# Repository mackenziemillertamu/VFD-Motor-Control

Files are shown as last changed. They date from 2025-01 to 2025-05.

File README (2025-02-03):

"Your project should have a README file that explains the project and what is contained in the repository"

Traditional motor control systems cannot adjust to varying load demands, resulting in poor energy efficiency, excessive heat generation, and premature component failure. Our project is to develop a Variable Frequency Drive (VFD) motor control system to adjust frequency and voltage to load demands. 

This github repository includes altium files, firmware code files, presentations pdfs, and report pdfs to act as a backup of our progess in the event of an emergency.

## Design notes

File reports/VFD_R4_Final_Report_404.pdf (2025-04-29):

# VFD Motor Controller

# Mackenzie Miller Andrew Nguyen Aidan Rader Ryan Regan

# CONCEPT OF OPERATIONS

### REVISION – 1 28 April 2025

### CONCEPT OF OPERATIONS

### FOR

## VFD Motor Controller

TEAM VFD MOTOR CONTROLLER

APPROVED BY:

_____________________________
Project Leader | Date

_____________________________
Prof. Lusher | Date

_____________________________
T/A | Date

Concept of Operations | Revision 1
VFD Motor Controller

II

### Change Record

Rev. | Date | Originator | Approvals | Description
0 | 9/15/2024 | VFD Motor Controller Team | | Draft Release
1 | 4/28/2025 | VFD Motor Controller Team | | Final Report Update

Concept of Operations | Revision 1

III

### Table of Contents

Table of Contents | III
List of Figures | IV

Concept of Operations | Revision 1

IV

### List of Figures

Concept of Operations | Revision 1

## 1. Executive Summary

The sponsor for this project is in need of a VFD motor controller for an AC induction motor. The VFD will control the speed and torque of the AC motor. This project will help to increase energy efficiency by ensuring that the motor isn’t running at a higher speed than necessary. It also makes the system more reliable and sustainable by decreasing mechanical stress.

A Variable Frequency Drive (VFD) is a device that controls the speed of an electric motor by varying the frequency of the delivered voltage. VFDs are useful because they improve the energy efficiency, reliability, safety, stability, and controllability of a motor. The goal of this project is to make a VFD motor controller that will efficiently control the seed and torque of an electric motor.

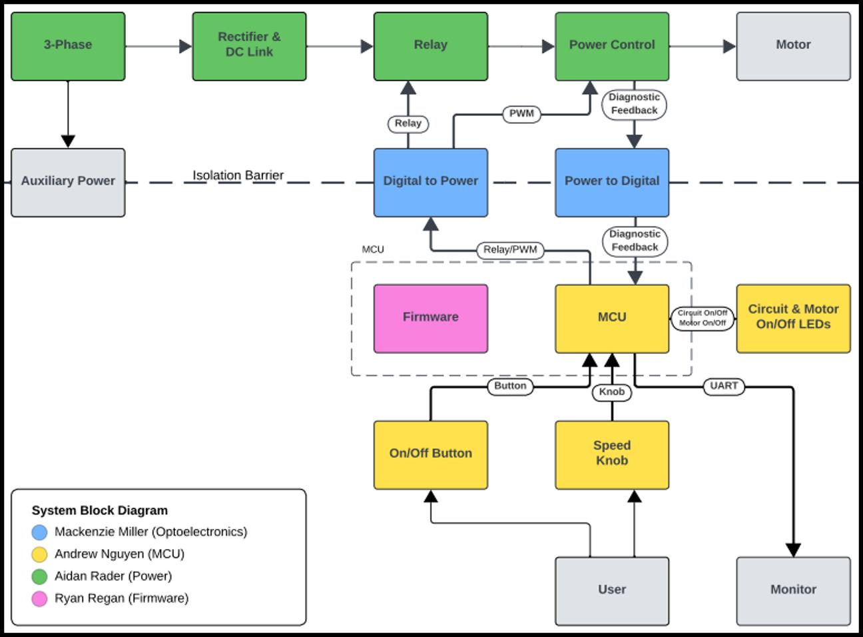
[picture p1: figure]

Figure 1: VFD Motor Controller Block Diagram

Concept of Operations | Revision 1

## 2. Introduction

### 2.1 Background

VFD motor controllers have several beneficial functionalities that can improve the quality of a system. A VFD motor controller regulates the speed and torque of electric motors by controlling the frequency and voltage supplied. The speed is controlled by varying the frequency of the supply of electricity. It also allows for more efficient systems. By running at certain speeds, the VFD can reduce the power consumed, allowing for energy to be saved. It also reduces stress on the motor by allowing for soft starting and stopping. The VFD also has a functionality allowing it to shut off the motor if something is shorted, overheating, or overloaded. The VFD will replace a fixed speed motor in a mechanical system.

### 2.2 Overview

While fixed speed motor controllers are still useful in some applications, more often than not a VFD motor controller is a better alternative. It offers all the functionality of a fixed speed motor controller while also being able to vary the speed and torque of the motor if needed. In this project, our team will work to create a Variable Frequency Drive to control motor speed. In addition, we will consider several different factors such as user interface for the drive, and implementation of the drive in a closed and open loop. This upgrade will improve the energy efficiency, reliability, safety, stability, and controllability of the motor.

### 2.3 Referenced Documents and Standards

“The Advantages of Frequency Drive Operation in Submersible Pumps.” Grundfos, www.grundfos.com/us/learn/ecademy/all-courses/the-sp-submersible-pump/the-advantages-of-frequency-drive-operation-in-submersible-pumps. Accessed 15 Sept. 2024.
By, and Dosupply. “What Do VFDS DO in HVAC Systems?: Do Supply Tech Support.” Do
Supply Tech Support | Information and Troubleshooting on Allen-Bradley, Eaton, GE
Fanuc, and More, 11 Aug. 2022, www.dosupply.com/tech/2022/08/11/what-do-vfds-do-in-hvac-systems/. (http://www.dosupply.com/tech/2022/08/11/what-do-vfds-do-in-hvac-systems/)

Hoffman, Theresa. “What Are the Benefits of a Variable Frequency Drive?” Wolf Automation,www.wolfautomation.com/blog/what-are-the-benefits-of-a-variable-frequency-drive/. Accessed 15 Sept. 2024.

“Variable Frequency Drive for Conveyor and Material Handling.” Variable Frequency Drive for Conveyor and Material Handling-Darwin Motion, darwinmotion.com/blogs/variable-frequency-drive-for-conveyor-and-material-

Concept of Operations | Revision 1

handling#:~:text=The%20use%20of%20a%20Variable,belt%20speed%2C%20reducin g%20energy%20consumption. Accessed 15 Sept. 2024.

IEEE 519-2014 Standard for Harmonics

Concept of Operations | Revision 1

## 3. Operating Concept

### 3.1 Scope

The VFD motor controller is intended to control the speed and torque of an AC motor by varying the frequency and voltage supplied. This project will use three phase power as the input that will be converted to DC and then transmitted to a microcontroller via optoelectronics and used to power a motor. The microcontroller also will send signals to the DC link, again using optoelectronics, that contain the desired frequency specified by the user on the user interface. This VFD shall be implemented to increase efficiency and save energy.

### 3.2 Operational Description and Constraints

The VFD motor controller is designed to vary the frequency and voltage supplied to an AC motor to control its speed and torque. It converts a three-phase AC input into DC using a rectifier and transmitting the power using a microcontroller.
- Microcontroller Function
- The microcontroller is responsible for generating pulse-width modulation (PWM) signals which are used to adjust the frequency and voltage supplied to the motor.
- The user can set the desired motor speeds via the user interface or the code itself. The microcontroller then ensures that the motor is running according to its specifications.
- Optoelectronics
- LED lights are used to communicate between the high-voltage power components and the low-voltage microcontroller. This ensures that the signals are safely transmitted.
- User Interface
- The microcontroller will have a potentiometer that allows the user to change the frequency of the three-phase PWM signal that is being output to the motor.
- While the PCB is plugged into a computer, opening the output terminal in MPLab will allow the user to view debug statements such as the potentiometer’s value, output duty cycles to phases A, B, and C, sine wave table step size, and desired output frequency of the PWM sine wave.
- Constraints:
- Sustainability
- Humidity, dust, and temperatures outside of the specified range can cause the VFD to malfunction.
- Noise levels
- The VFD is noise sensitive and is susceptible to external electrical noise, which could decrease the reliability of the system.

Concept of Operations | Revision 1
- Power
- The VFD requires stable three-phase AC power. Spikes or fluctuations could damage some of the system’s components.
- Mechanical wear and maintenance
- All parts of the VFD are subject to general mechanical wear and tear over time, especially if operated under high loads or in challenging environments.
- Cost and installation
- The VFD system can be expensive to produce, especially when considering large-scale applications. Consideration must be given to the specific needs of the project

### 3.3 System Description

The VFD motor controller is comprised of a DC link (includes a rectifier and DC bus), power controller, microcontroller, and optoelectronics. The DC link converts AC input into DC and minimizes the noise of the DC signal. The power controller controls the voltage. The microcontroller is used to produce PWM signals that will drive the motor. Optoelectronics allows for communication between the high voltage side and the low voltage microcontroller.
This is a four-person project, and the roles are be split into:
- Firmware:
- Write code in C with MPLAB that programs the microcontroller so that it functions with the rest of the VFD system according to desired specifications.
- Use a potentiometer to allow user to change the frequency of three-phase PWM signal.
- Print debug and feedback signals to UART console to allow for even further debugging.
- Test program on development board to ensure functionality then ensure proper integration with the project’s microcontroller.
- Optoelectronics
- The first part of the optoelectronics portion includes two isolation circuits. One of those takes digital signals in and directly converts them to analog. The second, being more complicated, takes analog input, then, using an optoisolator, the circuit converts the input to digital signals to be sent to the microcontroller. The analog side of the project works with very high voltage, while the digital side works with low voltage. Because of this, the two sides cannot be connected or the microcontroller will be overpowered and break, so the optoelectronics send signals and data across using light.
- The second part of the sensors portion is a constant current and voltage measurement. This will be done using a current sensing resistor, which has a

Concept of Operations | Revision 1

very small resistance, and a simple voltage divider circuit. These measurements will then be sent back to the firmware.
- Microcontroller:
- The MCU board is supplied by taking in the 120VAC from the wall and using an AC/DC converter to step it down to 15VDC. The voltage is then stepped down once more using the LM2595s-3.3 buck converter to a usable 3.3V that the MCU can handle. It receives feedback through low-voltage analog signals that represent voltage and current. The MCU will then send out PWM signals to the H bridge and power control system which are used to adjust the output voltage and frequency supplied to the motor. The board will also supply the optoelectronics subsystem with a common GND and 3.3V, and the power subsystem with a common GND, 15V, and 3.3V.
- Power:
- The rectifier takes in three-phase AC power and converts it into DC power. For each phase, there are parallel diodes acting as a one-way bridge for the current allowing it to flow in only one direction. To maintain the correct current polarity the diode opens and closes in sequence as the AC waveform alternates. The DC output is then filtered by capacitors within the DC link to provide a stable DC voltage for the microprocessor.
- The power control will take the DC power and the PWM signals and output three modified sign waves at 120 degrees to the motor. It will also output three measurement signals that can be used as diagnostic feedback: voltage, current, temperature
- The relay will take in a relay signal originating by the button press on the microcontroller and toggle the motor between on and off states.
- Converters will be used as part of auxiliary power to generate the necessary voltage levels for the different integrated chips. The two converters on the power PCB with be a 3.3 VDC to isolated 5 VDC converter and a 15 VDC to isolated 15 VDC.

### 3.4 Modes of Operations

There are two primary modes of operation for the variable frequency drive:
On: The motor receives 10-60Hz PWM signals depending on the position of the potentiometer located on the microcontroller PCB. The frequency of the PWM signals changes the speed of the motor.
Off: The relay is tripped, and the motor is no longer receiving any power.

### 3.5 Users

The potential user for our VFD would be a plant operator or manager. The goal is to have it set up to ensure a seamless installation and programming process for use in a closed or open

Concept of Operations | Revision 1

loop. It is assumed that a plant operator would know and understand what a VFD is and what it does. There will be simple controls that the user can change to make the VFD do what they want it to do such as a potentiometer for controlling the frequency of output signals, and a start/stop button.

### 3.6 Support

We plan to create a manual describing what the VFD does and how to use it. The VFD will support usage, programming, and debugging through MPLAB X IDE. It will allow the user to control the motor’s on/off function and its speed while showing the user several different variables including the measured motor speed from the tachometer.

Concept of Operations | Revision 1

## 4. Scenario(s)

### 4.1 HVAC

VFDs can be extremely useful in a Heating, Ventilation, and Air Conditioning (HVAC) system. VFDs can act as speed controllers for HVAC motors because they actively adjust the speed rate of those motors based on the building load demands. Without a VFD, an HVAC system will run at full power regardless of whether the system requires full power at that time. By running only as powerful as needed, energy and money are saved. Additionally, a VFD allows an HVAC motor to slowly get up to the full speed which is called a “soft start”. This lessens wear and tear on these HVAC motors, which helps them to last longer and saves money. VFDs can help HVAC systems to control temperature and pressure, among other measurements in a building, they help to save energy and extend the life of HVAC motors.

### 4.2 Conveyor Belt

In conveyors for production lines, a VFD allows an operator to control the belt's speed to match the production line's needs. This ensures that the belt is not moving too slow to decrease efficiency or too fast to risk injuring employees and consume copious amounts of energy. Wear and tear is also decreased by being able to run the belt at the most appropriate speed as to not overwork the parts or run the belt for too long. The slow start that a VFD can offer helps to reduce wear and tear on the conveyor parts so they can gradually get up to speed. There is the ability to gradually slow down the belt when turning off, which also extends the life of equipment. The VFD increases energy efficiency and reduces maintenance which both save money.

### 4.3 VFD Pump

VFDs are sought after for submersible pumps for several applications. The main benefit of a VFD in a water pump is the ability to keep a certain parameter constant. VFDs are commonly used in construction sites to keep groundwater at a constant level to build. The VFD does this by adjusting the speed of the motor controlling the water pump. Additionally, VFDs are useful in maintaining constant pressure in a water tank. VFDs are crucial in the operation of water pumps across many different disciplines because their speed control allows for constant parameters in the specified system.

Concept of Operations | Revision 1

## 5. Analysis

### 5.1 Summary of Proposed Improvements

Improvements:
- Extended life of parts: being able to vary frequency and torque help to reduce overloading equipment and, in turn, makes them last longer
- Increased efficiency: instead of a system having to run at a constant speed, a VFD allows the system to run only as fast as needed, which reduces energy consumption, and saves money
- Limits safety risks: having a system run at the proper speed and maintain a safe amount of torque helps decrease the risk of injury

### 5.2 Disadvantages and Limitations

Disadvantage:
- VFD can damage motor windings and bearings
- Can ruin insulation
- Creates harmonics (potentially interfering with communications and data processing)
- Can be very expensive
- Is prone to overheating if not in a properly ventilated area.
- Can create voltage spikes which could ruin the motor.

### 5.3 Alternatives

Alternatives to a VFD:
- Eddy Current Drive: induces a magnetic field that is adjustable to control the speed of a motor
- Soft Starters: Soft starters gradually increase the voltage to an AC motor during startup to reduce damage. They provide a more economical choice for applications where torque and speed control are only required during motor startup and stop.
- Cycloconverters: Cycloconverters convert the frequency of AC power from one frequency to another without having to convert to DC and back to AC. They are typically used in applications that require low speeds and high torque. This is a good alternative for when direct frequency conversion is more suitable than VFDs.

### 5.4 Impact

One environmental impact of a VFD is the ability to lower greenhouse gas emissions. By increasing the motor's energy efficiency through frequency adjustments to match load requirements, VFDs decrease the emissions released during the energy generation process.

Concept of Operations | Revision 1

A second environmental impact of a VFD is the degradation caused by mining the raw materials. While mining procures the rare metals needed for electronics, it also causes deforestation from the removal of forests, soil erosion from the disruption of the soil structure, and air pollution from the diesel emissions and dust particles generated by the machinery.

Another environmental impact of a VFD is the end-of-life disposal of electronic waste. Disposal of electronics can be challenging and, if done improperly, can contaminate soil and water with toxic metals. Alternatively, VFDs reduce this risk by reducing equipment wear, extending replacement intervals, and reducing disposal frequency.

A social impact of a VFD is the change in employment opportunities. The automation of the VFD reduces the need for operators who manually control the motor speed. Conversely, VFDs generate new roles including engineers who design the systems, miners who extract the raw materials, factory workers who assemble the components, and technicians who handle the maintenance.

Another social impact of a VFD is the safety risks. The VFD's automation of motor control within safe torque limits reduces the risk of accidents or injuries. However, if the VFD is improperly insulated or maintained, high voltages can pose a risk of electrical shock, and insulation breakdowns can pose a risk of short circuits and fire.

One ethical concern of a VFD is supply chain transparency. The raw materials for VFDs are often sourced from mines in countries with varying labor laws. In these mines, workers may face safety risks, including interacting with hazardous chemicals and dangerous machinery. Additionally, these mines should also avoid exploitative practices, including unfair compensation and unreasonable working hours.

A second ethical concern of a VFD is testing sufficiency. Before bringing a VFD to market, it should meet safety standards and demonstrate reliable operation. The testing process should include quality construction to prevent defects, comprehensive testing to identify defects, and clear documentation to resolve defects.

# VFD Motor Controller

# Mackenzie Miller Andrew Nguyen Aidan Rader Ryan Regan

# INTERFACE CONTROL DOCUMENT

### REVISION – 0 26 September 2024

### INTERFACE CONTROL DOCUMENT

### FOR

## VFD Motor Controller

PREPARED BY:

_____________________________
Author | Date

APPROVED BY:

_____________________________
Project Leader | Date

_____________________________
John Lusher II, P.E. | Date

_____________________________
T/A | Date

Interface Control Document | Revision - 0

II

### Change Record

Rev. | Date | Originator | Approvals | Description
0 | 9/26/2024 | VFD Motor Controller Team | | Draft Release
1 | 12/5/2024 | VFD Motor Controller Team | | Microcontroller and firmware descriptions updated
2 | 4/28/2025 | VFD Motor Controller Team | | Final Report Update

Interface Control Document | Revision - 0

III

### Table of Contents

Table of Contents | III
List of Tables | IV
List of Figures | V
No table of figures entries found | V

Interface Control Document | Revision - 0

IV

### List of Tables

Interface Control Document | Revision - 0

V

### List of Figures

No table of figures entries found.

Interface Control Document | Revision - 0

## 1. Overview

This Interface Control Document (ICD) for the VFD Motor Controller provides an overview of the requirements and specifications for a Variable Frequency Drive that will be used to control a motor and it’s speed. Created by Ryan Regan, Andew Nguyen, Mackenzie Miller, and Aidan Rader, this document describes the physical, electrical, thermal, and communication interfaces for the system.

Key Sections:
- Physical Interface: This section depicts the physical aspects of the VFD including weight, dimensions, and physical/spatial requirements.
- Thermal Interface: The VFD includes a thermal monitoring system using the VFO pin and ITRIP pins that will shut the system down if the temperature levels are too high
- Electrical Interface: The electrical specifications include motor power, DC supply voltage, and the microcontroller’s stepped-down voltage supply. The DC voltage will be regulated by an H-bridge, and optoelectronic circuits will be used to isolate the microcontroller from the high voltage section of the system.
- User Interface: The VFD’s firmware allows the user to control the on/off functionality of the system as well as the speed of the motor with a button and potentiometer. The microcontroller can be plugged into a computer to view other different diagnostic feedback variables from the system.
- Communication Protocols: Optoelectronics will be used for communication between the high-voltage power control and the low-voltage microcontroller. Additionally, the system will use UART for serial communication and will have USB connectivity for programming and debugging.

Interface Control Document | Revision - 0

## 2. References and Definitions

### 2.1 Definitions

AC | Alternating Current
DC | Direct Current
GUI | Graphical User Interface
ICD | Interface Control Document
MHz | Megahertz (1,000,000 Hz)
MCU | Micro Controller Unit
mA | Milliamp
mW | Milliwatt
N/A | Not Applicable
TBD | To Be Determined
VFD | Variable Frequency Drive

Interface Control Document | Revision - 0

## 3. Physical Interface

### 3.1 Weight

The VFD motor controller may weigh up to 6lbs. The motor itself may weigh up to 13lbs.

### 3.2 Dimensions

### 3.2.1 Dimension of Optoelectronics and Feedback

Component | Diameter | Length | Width | Height
Digital Isolator | N/A | 0.406” | 0.406” | 0.104”
Analog to Digital Optoisolator | N/A | 0.442” | 0.354” | 0.158”
Operational Amplifier | N/A | 0.382” | 0.25” | 0.400”
12 Pin Connector | N/A | 0.854” | 0.389” | 0.271”
8 Pin Connector | N/A | 1.089” | 0.447” | 0.272”

### 3.2.2 Dimensions of MCU

Component | Diameter | Length | Width | Height
dsPIC33CK256MP508 | N/A | 0.394” | 0.394” | 0.039”
LM2595s-3.3 Buck Converter | N/A | 0.400” | 0.180” | 0.450”
IRM 15-15 AC/DC Connector | N/A | 2.06” | 1.07” | 0.945”
20 Pin connector | N/A | 1.68” | 0.276” | 0.335”
5 Pin Connector | N/A | 0.314” | 0.433” | 0.370”
3 Pin Connector | N/A | 0.600” | 0.322” | 0.393”
Potentiometer | 0.236” (actuator) | 0.433” | 0.386” | 1.173”

The physical dimensions of the subsystem will be relative to the size of the user’s laptop and the size of the motor, both should not exceed the size of a standard tabletop.

### 3.2.3 Dimensions of Rectifier & DC Link

Component | Diameter | Length | Width | Height
VUE75-06NO7 | N/A | 1.850” | 1.193” | 0.799”
IKCM30F60GD | N/A | 1.417” | 0.827” | 0.201”
Capacitor(s) | N/A | TBD | TBD | TBD
Inductor(s) | N/A | TBD | TBD | TBD

Table 1: Optoelectronics and Feedback Dimensions

Table 2: MCU Dimensions

Table 3: Rectifier & DC Link Dimensions

Interface Control Document | Revision - 0

## 4. Thermal Interface

### 4.1 Temperature Sensing

The power control shall monitor the temperature via the VFO pin, and if the VFD temperature rises above a safe value, the ITRIP pin will automatically shut the project down to avoid damaging parts.

Interface Control Document | Revision - 0

## 5. Electrical Interface

### 5.1 Primary Input Power

The motor being used is 0.25HP producing 186.425W of power. The voltage supplied to the system is 295VDC which is then taken in by the H-bridge to generate a line-to-line voltage of 208V. 15VDC power is supplied to the MCU from the AC/DC power supply fed by the main power. This voltage will be stepped down to 3.3V for the MCU to use.

### 5.2 Voltage and Current Levels

Component | Voltage (V) | Current (mA)
dsPIC33CK | 3.3V | 50mA
IKCM30F60GD | 600V | 60A

### 5.3 Signal Interfaces

Pulse Width Modules will be sent from the microcontroller to the power control of the VFD project using optoelectronic circuitry to ensure the microcontroller does not come into contact with the high voltage in the power control.
Three phase voltage values will be sent to the microprocessor from the power control using optoelectronic circuitry to ensure that the microprocessor does not come into contact with the high voltage in the power control.

### 5.4 User Control Interface

One feature of the VFD’s microcontroller will be a potentiometer that allows the user to control the frequency of the three phase PWM’s sine wave by increasing the step size that the program uses to step through a sine wave table. Increasing the PWM signal’s frequency will increase the speed of the motor. The user will be able to change the frequency by turning a potentiometer. Another feature of the microcontroller is the start/stop button. This will give the user the option to turn the motor on and off without having to disconnect the system’s power. In addition to the physical user interface, the VFD will display several debug variables to the UART console in MPLAB X IDE when connected to a computer. The user will be able to view the voltage, current, and temperature in a UART console.

Table 4: Maximum Voltage and Current Values

Interface Control Document | Revision - 0
Pin | Function
1 | PWM1H
2 | GPIO
3 | PWM1L
4 | GPIO
9 | MCLR
11,32,50,70 | VSS
12,31,51,71 | VDD
17,22,39,44 | GPIO
19 | GPIO (Potentiometer)
24 | GPIO (LED 2)
25 | AVDD
26 | AVss
34 | Clock input
37 | GPIO (LED 1)
42 | GPIO (Relay)
60 | PGD1
61 | PGC1
68 | UART TX
69 | UART RX
75 | PWM3H
76 | PWM3L
78 | PWM2H
80 | PWM2L

Table 5: Pin interface for DSPIC33CK256MP508 Microcontroller

Interface Control Document | Revision - 0

## 6. Communications / Device Interface Protocols

### 6.1 Optoelectronic Communications

The high voltage power control of the VFD will communicate to the low voltage or MCU via optoelectronics, or light to ensure that the MCU is not overpowered by the 120 VAC in the analog power control side.

### 6.2 Firmware and MCU Communications

The microcontroller is programmed with C code through MPLab’s X IDE and will have several firmware implementations such as an on/off button’s functionality and a three-phase PWM wave’s frequency control.

### 6.3 Device Peripheral Interface

The MCU will use UART interface for serial communication between devices. This is what will allow a laptop to communicate with the microcontroller through USB connection.

### 6.4 Host Device

The C code shall be ran on MPLab’s X IDE, which should be downloaded on the users computer. This will be used to program the microcontroller and output any debug variables necessary while the system is running.

# VFD Motor Controller

# Mackenzie Miller Andrew Nguyen Aidan Rader Ryan Regan

# FUNCTIONAL SYSTEM REQUIREMENTS

### REVISION – 1 28 April 2025

### FUNCTIONAL SYSTEM REQUIREMENTS

### FOR

## VFD Motor Controller

PREPARED BY:

_____________________________
Author | Date

APPROVED BY:

_____________________________
Project Leader | Date

_____________________________
John Lusher, P.E. | Date

_____________________________
T/A | Date

Functional System Requirements | Revision - 1

II

### Change Record

Rev. | Date | Originator | Approvals | Description
0 | 9/26/2024 | VFD Motor Controller Team | | Draft Release
1 | 12/5/2024 | VFD Motor Controller Team | | Reference documents updated
2 | 4/28/2025 | VFD Motor Controller Team | | Final Report Update

Functional System Requirements | Revision - 1

III

### Table of Contents

Table of Contents | III
List of Tables | IV
List of Figures | V

Functional System Requirements | Revision - 1

IV

### List of Tables

Functional System Requirements | Revision - 1

V

### List of Figures

Functional Requirements Document | Revision 0
VFD Motor Control

## 1. Introduction

### 1.1. Purpose and Scope

The VFD motor controller is intended to control the speed and torque of an AC motor by varying the frequency and voltage supplied. This project will use three phase power as the input that will be converted to DC and then transmitted to a microcontroller via optoelectronics and used to power a motor. The microcontroller also will send signals to the DC link, again using optoelectronics, that contain the desired frequency. The VFD motor controller will come with a user interface that allows the user to input the frequency needed and start or stop the system as needed. This VFD shall be implemented to increase efficiency and save energy.

The following definitions differentiate between requirements and other statements.

Shall: | This is the only verb used for the binding requirements.
Should/May: These verbs are used for stating non-mandatory goals.
Will: | This verb is used for stating facts or declaration of purpose.

### 1.2. Responsibility and Change Authority

Briefly describe who has the responsibility for making sure the requirements are met (i.e., team leader) and who has the authority to make the changes (i.e., client and team leader).

Figure 1: Project Conceptual Image

Functional System Requirements | Revision - 1
Subsystem | Team Member
Optoelectronics & Monitoring | Mackenzie Miller
Microcontroller | Andrew Nguyen
Rectifier & DC Link | Aidan Rader
Firmware | Ryan Regan
Table 1: Subsystem Designations

Functional System Requirements | Revision - 1

## 2. Applicable and Reference Documents

### 2.1 Applicable Documents

The following documents, of the exact issue and revision shown, form a part of this specification to the extent specified herein:

Document Number | Revision/Release Date | Document Title
IEEE 519-2014 | 3/27/2014 | Standard for Harmonics
NFPA 70 Article 430 | 08/8/2023 | Motors, Motor Circuits and Controllers

### 2.2 Reference Documents

The following documents are reference documents utilized in the development of this specification. These documents do not form a part of this specification and are not controlled by their reference herein.

Document Number/ Publisher | Revision/Release Date | Document Title
Microsemi | Revision 0/11-03-2005 | DM330030 Datasheet
Microchip Technology | Revision 11/06-2022 | dsPIC33CK256MP508 Family Data Sheet
Texas Instruments | Revision 3/05-2016 | LM2595 SIMPLE SWITCHER® Power Converter 150-kHz 1-A Step-Down Voltage Regulator datasheet
Skyworks | Revision B/09-2023 | Si861x/2x Low-Power, Single- and Dual-Channel Digital Isolator
Infineon | Revision 2019-10-16 | Control Integrated POwer System (CIPOS™) IKCM30F60GD
IXYS | Revision 2021 | VUE75-06NO7
Mean Well | Revision 10-30-2024 | IRM-15 series Datasheet

### 2.3 Order of Precedence

In the event of a conflict between the text of this specification and an applicable document cited herein, the text of this specification takes precedence without any exceptions.

All specifications, standards, exhibits, drawings or other documents that are invoked as “applicable” in this specification are incorporated as cited. All documents that are referred to within an applicable report are for guidance and information only, except ICDs that have their relevant documents considered to be incorporated as cited.

Table 2: Applicable Documents

Table 3: Reference Documents

Functional System Requirements | Revision - 1

## 3. Requirements

### 3.1 System Definition

The VFD motor controller is comprised of a DC link (includes a rectifier and DC bus), power controller, microcontroller, and optoelectronics. The DC link converts AC input into DC and minimizes the noise of the DC signal. The power controller controls the voltage. The microcontroller is used to produce PWM signals that will drive the motor. Optoelectronics allows for communication between the high voltage side and the low voltage microcontroller.
This is a four-person project split into these roles:

Firmware (Ryan Regan):
Write code in C using MPLab X IDE that programs the microcontroller so that it functions with the rest of the VFD system according to desired specifications. In other words, program a potentiometer to allow user to change the frequency of a three-phase PWM signal. The firmware will also implement debug statements that output to MPLAB X IDE’s UART console to allow user to view different variables as the program is running. Before integrating with the microcontroller and other subsystems, the firmware will be tested on a development board to ensure functionality.

Optoelectronics (Mackenzie Miller):
The first part of the sensors portion includes two optoelectronic circuits. One of those takes digital signals in and directly converts them to analog. The second, being more complicated, takes analog input, then, using an opto-isolator, the circuit converts the input to digital signals to be sent to the microcontroller. The analog side of the project works with very high voltage, while the digital side works with low voltage. Because of this, the two sides cannot be connected or the microcontroller will be overpowered and break, so the optoelectronics send signals and data across using light. The second part of the sensors portion is a constant current and voltage measurement. This will be done using a current sensing resistor, which has a very small resistance, and a simple voltage divider circuit. These measurements will then be sent back to the firmware. Finally, there will be a tachometer that measures the RPMs of the motor that is also sent to the firmware.

Microcontroller (Andrew Nguyen):
The MCU is supplied by the 15 VDC from the AC power supply fed by the main power. The voltage will then be stepped down to a usable 3.3V. It receives feedback through low-voltage analog signals that represent voltage and current. The MCU will then send out PWM signals to the H bridge and power control system which are used to control the inverter stage of the VFD which helps to adjust the output voltage and frequency supplied to the motor.

Rectifier and DC Link (Aidan Rader):

Functional System Requirements | Revision - 1

The rectifier takes in three-phase AC power and converts it into DC power. For each phase, there are parallel diodes acting as a one-way bridge for the current allowing it to flow in only one direction. To maintain the correct current polarity the diode opens and closes in sequence as the AC waveform alternates. The DC output is then filtered by capacitors within the DC link to provide a stable DC voltage for the microprocessor.

### 3.2 Characteristics

### 3.2.1 Functional / Performance Requirements

### 3.2.1.1 Speed and Torque Requirement

The 0.25HP VFD motor shall run up to 1800RPM. The torque requirement for this is 73lb-ft of torque.

### 3.2.1.2 Frequency Requirement

The VFD motor controller shall be able to handle frequencies from 5Hz to 60Hz.

Figure 2: Block Diagram of System

Functional System Requirements | Revision - 1

Rationale: American standard frequency for alternating current

### 3.2.1.3 Temperature Requirement

The VFD motor controller shall be able to operate at temperatures ranging from 0°C to 70°C.
Rationale: Commercial temperature rating standards

### 3.2.2 Physical Characteristics

### 3.2.2.1 System Components

The system shall consist of three printed circuit boards (PCBs) connected by wires.

### 3.2.3 Electrical Characteristics

### 3.2.3.1 Inputs

The presence or absence of any combination of the input signals in accordance with ICD specifications applied in any sequence shall not damage the VFD motor controller, reduce its life expectancy, or cause any malfunction, either when the unit is powered or when it is not.

No sequence of command shall damage the VFD, reduce its life expectancy, or cause any malfunction.

Rationale: By design, should limit the chance of damage or malfunction by user/technician
error.

### 3.2.3.2 Input Voltage Level

The input voltage level for the VFD shall be three phase 120 VAC.
Rationale: VFD specification, Sponsor

### 3.2.3.3 Input Noise and Ripple

The maximum ripple allowed on the dsPIC33CK is 165mV peak to peak.
Rationale: The specifications from the dsPIC33CK datasheet at 3.3V

### 3.2.3.4 External Commands

The VFD Motor Control Team shall document all external commands in the appropriate ICD.
Rationale: The ICD will capture all interface details from the low level electrical to the high-level packet format.

### 3.2.3.5 Visual Output

The VFD shall include a Graphical User Interface that displays output measurements.
Rationale: Provides the ability to see the outputs when VFD is running

Functional System Requirements | Revision - 1

### 3.2.3.6 Connectors

The VFD shall use terminal blocks for all power and signal connections to ensure secure and vibration-resistant connections.
Rationale: Noise must be limited to maintain signal integrity

### 3.2.3.7 Failure Propagation 3.2.3.7.1 Overtemperature Shutdown

The VFD shall have a sensor that automatically shuts the system down if the temperature rises above 70 degrees Celsius.

### 3.2.3.8 Built in Test (BIT)

The VFD shall have an internal subsystem that will generate test signals and evaluate the VFD responses and determine if there is a failure.

### 3.2.3.9 Digital to Power Continuity

The digital to power opto-isolators shall have a voltage of 0V across each component when measuring from input to output.

### 3.2.3.10 Power to Digital Continuity

The power to digital opto-isolators shall have a voltage of 0V across each component when measuring from input to output.

3.2.3.11 15 VDC to Isolated 15 VDC Conversion
Power converters shall convert 15 VDC to isolated 15 VDC.

3.2.3.12 15 VDC to 3.3 VDC Conversion
Power converters shall convert 15 VDC to 3.3 VDC.

3.2.3.13 3.3 VDC to Isolated 5 VDC Conversion
Power converters shall convert 3.3 VDC to isolated 5 VDC.

### 3.2.3.14 Low Voltage Auxiliary Power

System shall convert 15 VDC to isolated 15 VDC , 3.3 VDC, and isolated 5 VDC.

3.2.3.15 120 VAC to 15 VDC Conversion
Power converters shall convert 120 VAC to isolated 15 VDC.

3.2.3.16 120 VAC Auxiliary Power
System shall convert 120 VAC to 15 VDC, isolated 15 VDC , 3.3 VDC, and isolated 5 VDC.

### 3.2.3.17 Relay

Relay shall toggle the motor with the relay signal.

### 3.2.3.18 Relay Signal Isolation

Digital to power shall convert the relay signal from 3.3 VDC to 5 VDC.

Functional System Requirements | Revision - 1

### 3.2.3.19 Relay Signal Generation

MCU shall toggle the relay signal to 3.3 VDC with the button signal.

### 3.2.3.20 Firmware Relay Signal Generation

Dev board shall toggle the relay signal to 3.3 VDC with the button signal.

### 3.2.3.21 Button Signal Generation

Button shall toggle the button signal to 3.3 VDC with a button press.

### 3.2.3.22 On/Off Button

System shall toggle the motor between on and off state with a button press.

3.2.3.23 120 VAC to 112 VDC Rectification
Rectifier shall convert 120 VAC to 112 VDC.

3.2.3.24 120 VAC to 112 VDC Rectification
Rectifier shall convert 120 VAC to 112 VDC.

### 3.2.3.25 Power Control

Power control shall invert three high and three low 5 VDC PWM signals into three modified sine waves.

### 3.2.3.26 PWM Signal Isolation

Digital to power shall convert three high and three low PWM signals from 3.3 VDC to 5 VDC.

### 3.2.3.27 PWM Signal Generation

MCU shall generate three high and three low 3.3 VDC PWM signals with the knob signal.

### 3.2.3.28 Knob Signal Generation

Rotating potentiometer changes frequency to speed up and slow down motor.

### 3.2.3.29 Firmware PWM Signal Generation

Dev board shall generate three high and three low 3.3 VDC PWM signals with the knob signal.

### 3.2.3.30 Firmware Knob Signal Generation

Rotating dev board potentiometer changes frequency to speed up and slow down motor.

### 3.2.3.31 Low Voltage PWM Control

System shall change the motor speed with the knob signal.

3.2.3.32 112 VDC PWM Control
System shall change the motor speed with the knob signal.

### 3.2.3.33 Motor On/Off Signal Generation

MCU shall toggle the motor on/off LED signal to 3.3 VDC with the button signal.

### 3.2.3.34 Motor On/Off LED

Functional System Requirements | Revision - 1

System shall toggle the motor on/off LED between on and off states with the motor on/off signal.

### 3.2.3.35 System On/Off Signal Generation

MCU shall toggle the circuit on/off LED signal to 3.3 VDC when the board receives power.

### 3.2.3.36 System On/Off LED

System shall toggle the circuit on/off LED when the board is connected to power with the circuit on/off signal

### 3.2.3.37 Firmware Motor On/Off LED Signal Generation

Firmware shall toggle the dev board's on/off LED signal to 3.3 VDC with the button signal.

### 3.2.3.38 Firmware Motor On/Off LED

Firmware shall toggle the dev board's on/off LED between on and off states with the motor on/off signal.

### 3.2.3.39 Firmware System LED Signal Generation

Firmware shall toggle the dev board's on/off LED signal to 3.3 VDC when the board receives power.

### 3.2.3.40 Firmware System LED

Firmware shall toggle the dev board's on/off LED when the board is connected to power with the circuit on/off signal

### 3.2.3.41 Computer Display

MCU will display diagnostic feedback information to the UART console on a computer running MPLAB X IDE

### 3.2.3.42 Diagnostic Feedback Signal Isolation

Diagnostic feedback circuit shall transport the voltage, current, and temperature signals from across the isolation barrier to the MCU.

### 3.2.3.43 Diagnostic Feedback Signal Generation

Power Control shall generate 60 VDC voltage, current, and temperature feedback signals.

### 3.2.3.44 Diagnostic Feedback

System shall send the voltage, current, and temperature signals to the computer display.

Functional System Requirements | Revision - 1

## Appendix A: Acronyms and Abbreviations

BIT | Built-In Test
CCA | Circuit Card Assembly
EMC | Electromagnetic Compatibility
EMI | Electromagnetic Interference
EO/IR | Electro-optical Infrared
FOR | Field of Regard
FOV | Field of View
GPS | Global Positioning System
GUI | Graphical User Interface
Hz | Hertz
ICD | Interface Control Document
kHz | Kilohertz (1,000 Hz)
LCD | Liquid Crystal Display
LED | Light-emitting Diode
mA | Milliamp
MHz | Megahertz (1,000,000 Hz)
MTBF | Mean Time Between Failure
MTTR | Mean Time To Repair
mW | Milliwatt
PCB | Printed Circuit Board
RMS | Root Mean Square
TBD | To Be Determined
TTL | Transistor-Transistor Logic
USB | Universal Serial Bus
VFD | Variable Frequency Drive
VME | VERSA-Module Europe

Functional System Requirements | Revision - 1

## Appendix B: Definition of Terms

# VFD Motor Controller

# Mackenzie Miller Andrew Nguyen Aidan Rader Ryan Regan

# EXECUTION AND VALIDATION PLAN

### REVISION – 1 28 April 2025

## Execution Plan

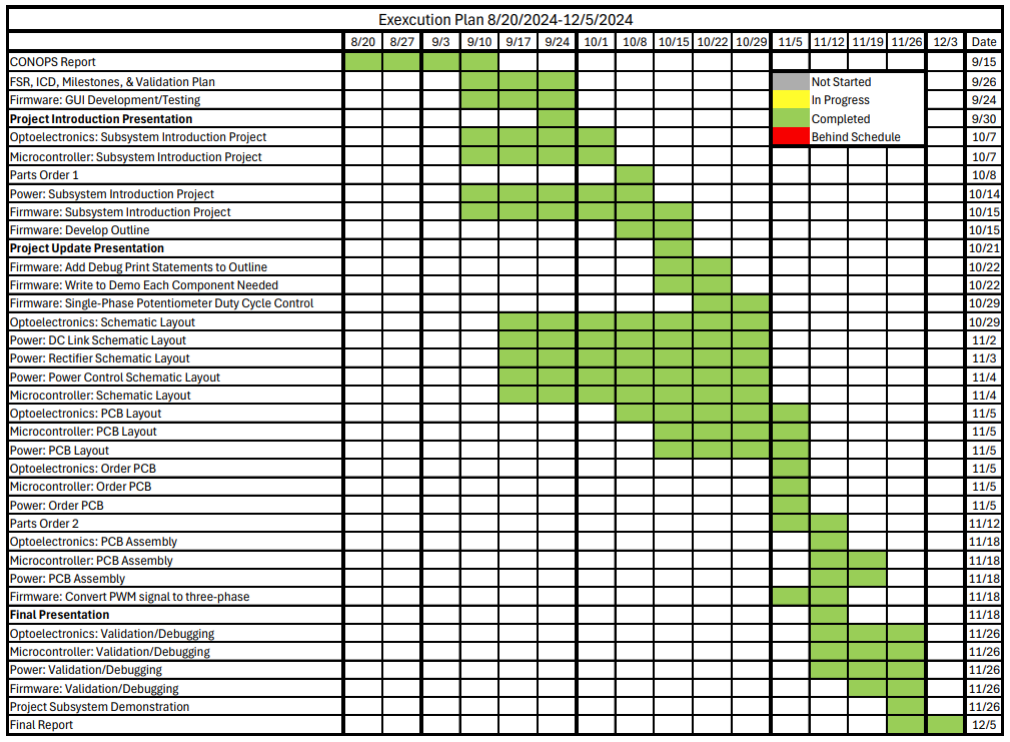
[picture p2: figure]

Figure 1: Execution Plan Fall 2024

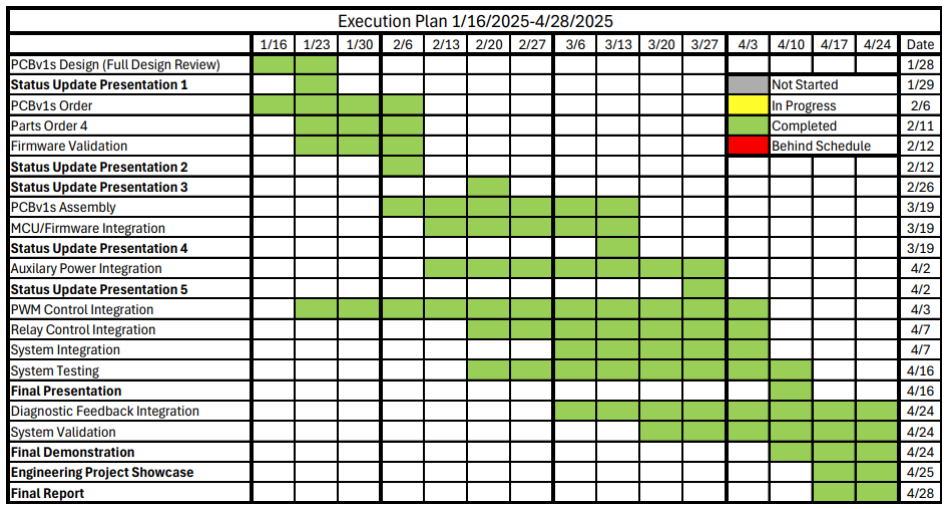
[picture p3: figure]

## Validation Plan

Paragraph # | Test Name | Success Criteria | Methodology | Status | Responsible Engineer(s)
3.2.3.11 | 15 VDC to Isolated 15 VDC Conversion | Power converters shall convert 15 VDC to isolated 15 VDC. | Apply 15 VDC input using a DC power supply. Verify 15 VDC output using an oscilloscope. | Tested | Aidan
3.2.3.12 | 15 VDC to 3.3 VDC Conversion | Power converters shall convert 15 VDC to 3.3 VDC. | Apply 15 VDC input using a DC power supply. Verify 3.3 VDC output using an oscilloscope. | Tested | Drew
3.2.3.13 | 3.3 VDC to Isolated 5 VDC Conversion | Power converters shall convert 3.3 VDC to isolated 5 VDC. | Apply 3.3 VDC input using a DC power supply. Verify 5 VDC output using an oscilloscope. | Tested | Aidan
3.2.3.14 | Low Voltage Auxiliary Power | System shall convert 15 VDC to isolated 15 VDC , 3.3 VDC, | Apply 15 VDC input using a DC power supply. Verify 15 VDC , 3.3 VDC, and 5 | Tested | Mackenzie, Drew, Aidan

Figure 2: Execution Plan Spring 2025

| and isolated 5 VDC. | VDC outputs using an oscilloscope.
3.2.3.15 | 120 VAC to 15 VDC Conversion | Power converters shall convert 120 VAC to isolated 15 VDC. | Apply 120 VAC input using a 120 VAC outlet. Verify 15 VDC output using an oscilloscope. | Tested | Drew
3.2.3.16 | 120 VAC Auxiliary Power | System shall convert 120 VAC to 15 VDC, isolated 15 VDC , 3.3 VDC, and isolated 5 VDC. | Apply 120 VAC input using a 120 VAC outlet. Verify 15 VDC, 15 VDC , 3.3 VDC, and 5 VDC outputs using an oscilloscope. | Tested | Mackenzie, Drew, Aidan
3.2.3.17 | Relay | Relay shall toggle the motor with the relay signal. | Apply 15 VDC coil voltage, 10 VDC contact voltage, and 5 VDC relay signal using a DC power supply. Verify 10 VDC output using an oscilloscope. | Tested | Aidan
3.2.3.18 | Relay Signal Isolation | Digital to power shall convert the relay signal from 3.3 VDC to 5 VDC. | Apply 5 VDC supply voltage, 3.3 VDC supply voltage, and 3.3 VDC relay signal using a DC power supply. Verify 5 VDC output using an oscilloscope. | Tested | Mackenzie
3.2.3.19 | Relay Signal Generation | MCU shall toggle the relay signal to 3.3 VDC with the button signal. | Apply 3.3 VDC supply voltage and 3.3 VDC button signal using a DC power supply. Verify 3.3 VDC output using an oscilloscope. | Tested | Drew, Ryan
3.2.3.20 | Firmware Relay Signal Generation | Dev board shall toggle the relay signal to 3.3 | (On the dev board) Apply 3.3 VDC supply voltage and 3.3 VDC button signal using | Tested | Ryan

| VDC with the button signal. | a DC power supply. Verify 3.3 VDC output using an oscilloscope.
3.2.3.21 | Button Signal Generation | Button shall toggle the button signal to 3.3 VDC with a button press. | Apply 3.3 VDC supply voltage using a DC power supply and initiate a button press. Verify 3.3 VDC output using an oscilloscope. | Tested | Drew
3.2.3.22 | On/Off Button | System shall toggle the motor between on and off state with a button press.

Apply 15 VDC coil
voltage, 10 VDC
contact voltage, 5
VDC supply voltage,
and 3.3 VDC supply
voltage using a DC
power supply.
Initiate one button
press and later a
second button
press. Verify the
motor rotates after
the first button
press and stops
after the second
button press using a
video.
Tested | All
3.2.3.23 | 10 VAC to 12 VDC Rectification | Rectifier shall convert 120 VAC to 112 VDC. | Apply 120 VAC input using a 120 VAC outlet. Verify 112 VDC output using an oscilloscope. | Tested | Aidan
3.2.3.24 | 120 VAC to 112 VDC Rectification | Rectifier shall convert 120 VAC to 112 VDC. | Apply 120 VAC input using a 120 VAC outlet. Verify 112 VDC output using an oscilloscope. | Tested | Aidan
3.2.3.25 | Power Control | Power control shall invert three high and three low 5 VDC PWM | Apply 40 VDC bus voltage and 15 VDC supply voltage using a DC power supply. Apply three high | Tested | Aidan

signals into
three
modified sine
waves.

and three low 5 VDC
PWM signals at
120˚ phase shifts
using a function
generator. Verify
three modified sine
waves at 120˚
phase shifts using
an oscilloscope.
3.2.3.26 PWM Signal Isolation

Digital to
power shall
convert three
high and three
low PWM
signals from
3.3 VDC to 5
VDC.

Apply isolated 5 VDC
supply voltage and
3.3 VDC supply
voltage using a DC
power supply.
Apply three high
and three low 3.3
VDC PWM signals at
120˚ phase shifts
using a function
generator. Verify
three high and
three low 5 VDC
PWM signals at
120˚ phase shifts
using an
oscilloscope.
Tested | Mackenzie
3.2.3.27 | PWM Signal Generation | MCU shall generate three high and three low 3.3 VDC PWM signals with the knob signal. | Apply 3.3 VDC supply voltage and 3.3 VDC speed knob signal using a DC power supply. Verify three high and three low 3.3 VDC PWM signals at 120˚ phase shifts using an oscilloscope. | Tested | Drew, Ryan
3.2.3.28 | Knob Signal Generation | Rotating potentiometer changes frequency to speed up and slow down motor. | Oscilloscope each signal output, spin knob and ensure the motor speed varies as expected. | Tested | Drew, Ryan

3.2.3.29 | Firmware PWM Signal Generation | Dev board shall generate three high and three low 3.3 VDC PWM signals with the knob signal. | (On dev board) Apply 3.3 VDC supply voltage and 3.3 VDC speed knob signal using a DC power supply. Verify three high and three low 3.3 VDC PWM signals at 120˚ phase shifts using an oscilloscope. | Tested | Ryan
3.2.3.30 | Firmware Knob Signal Generation | Rotating dev board potentiometer changes frequency to speed up and slow down motor. | (On dev board) Oscilloscope each signal output, spin knob and ensure the motor speed varies as expected. | Tested | Ryan
3.2.3.31 | Low Voltage PWM Control | System shall change the motor speed with the knob signal. | Apply 40 VDC bus voltage, 15 VDC supply voltage, isolated 5 VDC supply voltage and 3.3 VDC supply voltage using a DC power supply. Verify the motor rotates at a different speed after a knob turn using a video. | Tested | All
3.2.3.32 | 112 VDC PWM Control | System shall change the motor speed with the knob signal. | Apply 112 VDC bus voltage, 15 VDC supply voltage, isolated 5 VDC supply voltage and 3.3 VDC supply voltage using a DC power supply. Verify the motor rotates at a different speed | Untested | All

after a knob turn using a video.

3.2.3.33 | Motor On/Off Signal Generation | MCU shall toggle the motor on/off LED signal to 3.3 VDC with the button signal. | Directly inject 15V to MCU and use multimeter at the motor LED via. | Tested | Drew, Ryan
3.2.3.34 | Motor On/Off LED | System shall toggle the motor on/off LED between on and off states with the motor on/off signal. | Directly inject 15V to MCU, then press relay toggle button and ensure the motor LED toggles. | Tested | Drew, Ryan
3.2.3.35 | System On/Off Signal Generation | MCU shall toggle the circuit on/off LED signal to 3.3 VDC when the board receives power. | Directly inject 15V to MCU and use multimeter at the system LED via. | Tested | Drew, Ryan
3.2.3.36 | System On/Off LED | System shall toggle the circuit on/off LED when the board is connected to power with the circuit on/off signal | Directly inject 15V to MCU and ensure the system LED turns on. | Tested | Drew, Ryan
3.2.3.37 | Firmware Motor On/Off LED Signal Generation | Firmware shall toggle the dev board's on/off LED signal to 3.3 VDC with the button signal. | Directly inject 15V to dev board and use multimeter at the motor LED via. | Tested | Ryan

3.2.3.38 | Firmware Motor On/Off LED | Firmware shall toggle the dev board's on/off LED between on and off states with the motor on/off signal. | Directly inject 15V to dev board, then press relay toggle button and ensure the motor LED toggles. | Tested | Ryan
3.2.3.39 | Firmware System LED Signal Generation | Firmware shall toggle the dev board's on/off LED signal to 3.3 VDC when the board receives power. | Directly inject 15V to dev board and use multimeter at the system LED via. | Tested | Ryan
3.2.3.40 | Firmware System LED | Firmware shall toggle the dev board's on/off LED when the board is connected to power with the circuit on/off signal | Directly inject 15V to dev board and ensure the system LED turns on. | Tested | Ryan
3.2.3.41 | Computer Display | MCU will display diagnostic feedback information to the UART console on a computer running MPLAB X IDE. | Connect system to MPLAB X IDE using a laptop and USB-UART cable. Verify diagnostic print statements are being output to UART console. | Untested | Drew, Ryan
3.2.3.42 | Diagnostic Feedback Signal Isolation | Diagnostic feedback circuit shall transport the voltage, current, and temperature signals from | Apply 15 VDC supply voltage, isolated 15 VDC supply voltage, and three 15 VDC feedback signals using a DC power supply. Verify three | Untested | Mackenzie

| across the isolation barrier to the MCU. | 15 VDC outputs using an oscilloscope.
3.2.3.43 | Diagnostic Feedback Signal Generation | Power Control shall generate 60 VDC voltage, current, and temperature feedback signals. | Apply 40 VDC bus voltage and 15 VDC supply voltage using a DC power supply. Apply three high and three low 5 VDC PWM signals at 120˚ phase shifts using a function generator. Verify three 60 VDC outputs using an oscilloscope. | Untested | Aidan
3.2.3.44 | Diagnostic Feedback | System shall send the voltage, current, and temperature signals to the computer display. | Each feedback signal will be verified through the UART console output. | Untested | All

# VFD Motor Controller

# Mackenzie Miller Andrew Nguyen Aidan Rader Ryan Regan

# SUBSYSTEM REPORT

### REVISION – 1 28 April 2025

### SUBSYSTEM REPORT

### FOR

## VFD Motor Controller

PREPARED BY:

_____________________________
Author | Date

APPROVED BY:

_____________________________
Project Leader | Date

_____________________________
John Lusher, P.E. | Date

_____________________________
T/A | Date

Subsystem Report | Revision - 1

II

### Change Record

Rev. | Date | Originator | Approvals | Description
0 | 12/5/2024 | VFD Motor Controller Team | | Draft Release
1 | 4/28/2025 | VFD Motor Controller Team | | Final Report Update

Subsystem Report | Revision - 1

III

### Table of Contents

Table of Contents | III
List of Tables | IV
List of Figures | V

Subsystem Report | Revision - 1

IV

### List of Tables

Subsystem Report | Revision - 1

V

### List of Figures

Subsystem Report | Revision - 0

## 1. Introduction

The VFD motor controller is designed to regulate the speed and torque of an AC motor by adjusting the frequency and voltage it receives. This project utilizes three-phase power as the input, which will be converted to DC and transmitted a microcontroller to power the motor. The microcontroller will also send and receive signals, via optoelectronics, to the DC link to deliver the user-specified frequency set through the user interface. The VFD is intended to enhance efficiency and conserve energy.

Subsystem Report | Revision - 1

## 2. Optoelectronics Subsystem Report

### 2.1. Subsystem Introduction

The optoelectronics subsystem of the VFD serves as the go between for the microcontroller and the motor and power electronics. The microcontroller and high voltage side cannot encounter one another because the microcontroller operates at 3.3V, and the power electronics and motor operate at 120 VAC from the wall. Optoelectronics help transport voltages from the power control to the microcontroller and PWMs from the microcontroller to the power control.

### 2.2. Subsystem Details

The power to digital circuitry of this subsystem includes three circuits that convert signals that represent the voltage, current, and temperature of the system that are received to around 15V so the microcontroller (MCU) can process them. The first circuit takes the output of the DC rectifier, the second circuit is for the current and voltage monitoring, and the third circuit is for temperature control. These values are to be processed by the MCU and displayed on a UART console so the system can be monitored. These measurements are transported across an isolation barrier using light via emitters and receivers made into an integrated circuit. Below, in Figure 1, one of the circuits can be seen. The PCB realization of this is seen in Figure 3.

There are also three circuits that take pulse width modules (PWMs) in and transport them across another isolation barrier. The three isolators have been separated as follows: the first one transports PWM 1H and 1L and the relay signal, the second transports 2H and 2L, and the third is for 3H and 3L. The six PWMs are created by the MCU and are sent out at 3.3V. The isolators take in 3.3V and output the same PWMs at 5V to the power side. This segment is necessary in order to maintain the integrity of separating the power and digital sides. The schematic of this circuit can be seen below in Figure 2. The PCB realization of this is seen in Figure 4.

In the beginning of this project, there was to be a tachometer as a part of this subsystem, but near the end, it was cut due to timing. Had there been two or three more weeks, there could have been a tachometer to measure the revolutions per minute (RPMs) of the motor. This is not necessary for the completion of the project, but it would have been an interesting additional feature.

These circuits are executed on a printed circuit board (PCB) which yields a very compact design with many components.

Subsystem Report | Revision - 1

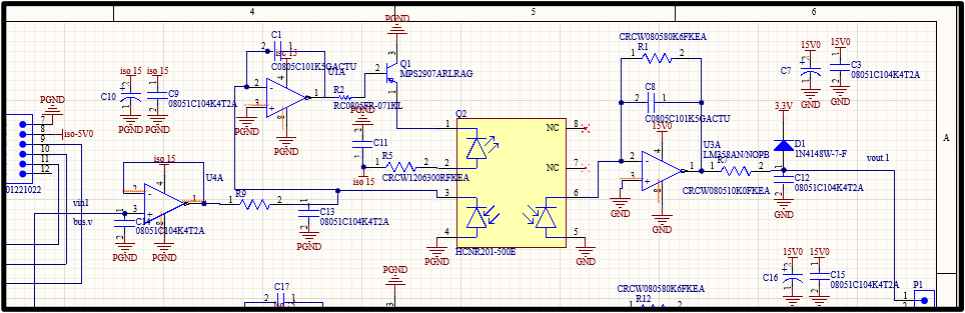
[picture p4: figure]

Figure 1: Power to Digital Schematic

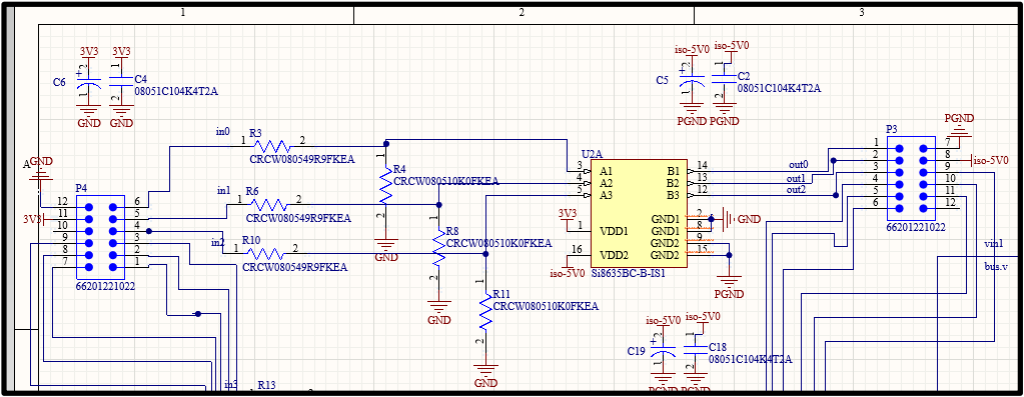
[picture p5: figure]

Figure 2: Digital to Power Schematic

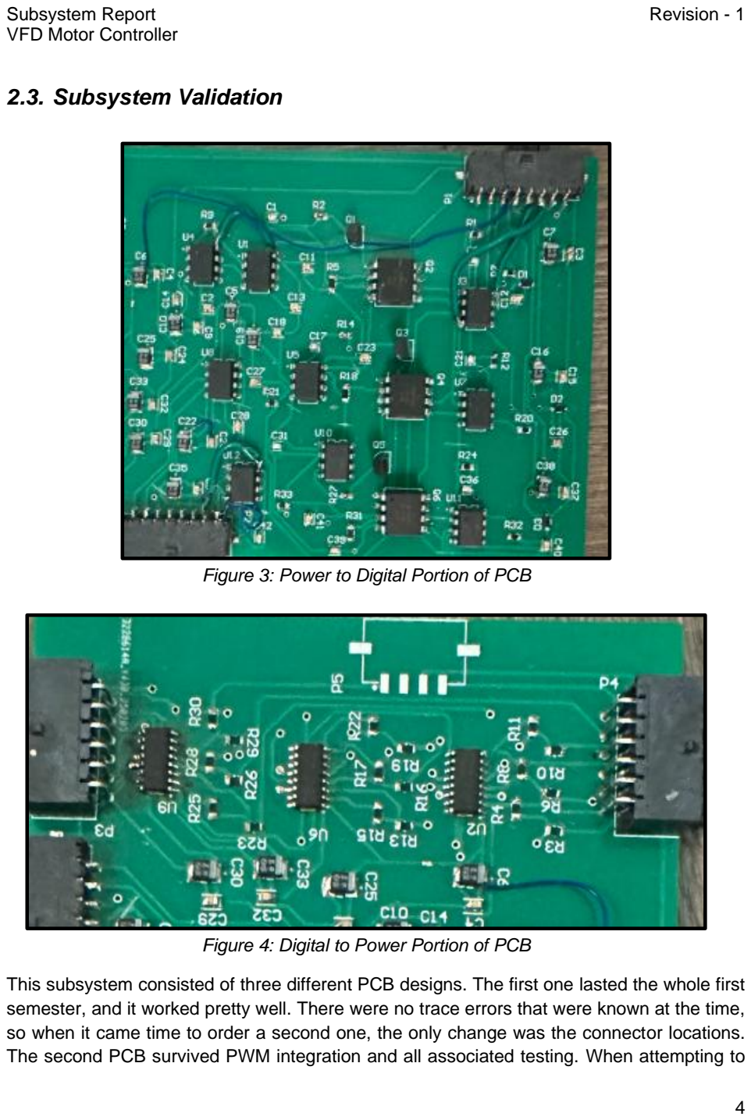
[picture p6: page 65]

Subsystem Report | Revision - 1

### 2.3. Subsystem Validation

This subsystem consisted of three different PCB designs. The first one lasted the whole first semester, and it worked pretty well. There were no trace errors that were known at the time, so when it came time to order a second one, the only change was the connector locations. The second PCB survived PWM integration and all associated testing. When attempting to

Figure 3: Power to Digital Portion of PCB

Figure 4: Digital to Power Portion of PCB

Subsystem Report | Revision - 1

test auxiliary power, a large voltage drop was discovered on this subsystem. The auxiliary power went through the power and MCU boards successfully, and this board was the final link. Based on this, the opto board was thought to be the issue. Along with this problem, the operational amplifiers (op-amps) were getting extremely hot. Originally, it was thought that a capacitor went out and was causing a short. The problem, however, was much larger than that. The Vcc and GND pins on each of nine op-amps were switched which caused the large voltage drop and essentially circuit failure. A third PCB was designed to fix this problem, but an incorrect version of the files, possibly unsaved, was submitted which led to a bad board being printed. Due to the short amount of time left in the semester, the best option available was to cut the incorrect traces with a knife and externally connect the Vcc and GND the correct way. This can be seen in Figure 5 below.

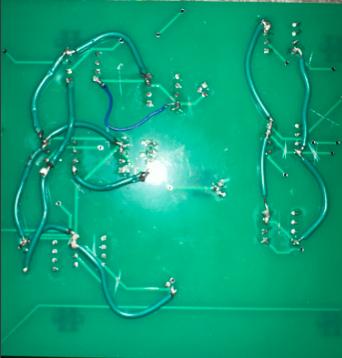
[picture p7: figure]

Figure 5: Cut Traces and External Wires to Fix Op-Amps

### 2.3.1. Digital to Power Isolation Validation

The first part of this subsystem that was tested and then integrated was the PWM isolation. When this portion was tested last semester, the isolators fried due to a testing error, so the parts were replaced and tested with PWMs coming out of the development (dev) board. The purpose of this board was to bypass the MCU until it was ready. The first time the opto PCB was connected to the dev board for the PWM input, it worked perfectly. The 3.3V input PWMs were converted to 5V PWM wave outputs for all three phases high and low. When it came time to test this with the MCU, the same result was observed. With the MCU, the input PWMs

Subsystem Report | Revision - 1

were 3.4V, and the outputs were 6.0V to 6.2V as seen in Figures 6 and 7. This is slightly higher than expected, but it was within the requirements, so these results were successful.

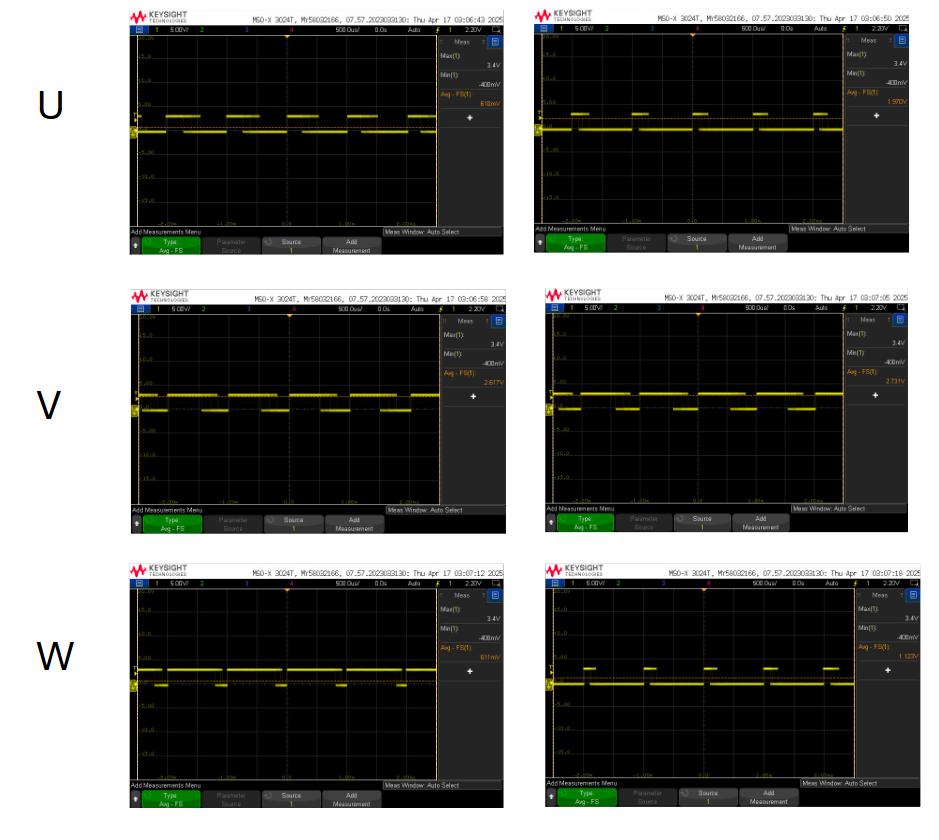
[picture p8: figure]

Figure 6: PWM input – Before Isolation

Subsystem Report | Revision - 1

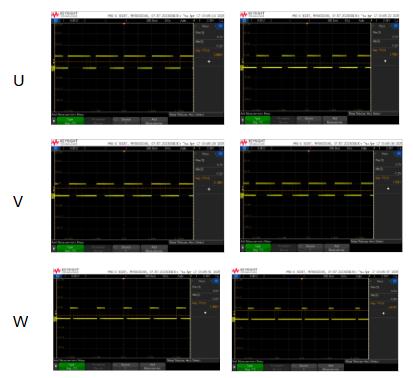
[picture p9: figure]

Figure 7: PWM Output – After Isolation

Subsystem Report | Revision - 1
PWM Input Voltage | PWM Output Voltage
PWM 1H – 3.4V | PWM 1H – 6.2V
PWM 1L – 3.4V | PWM 1L – 6.2V
PWM 2H – 3.4V | PWM 2H – 6.0V
PWM 2L – 3.4V | PWM 2L – 6.2V
PWM 3H – 3.4V | PWM 3H – 6.2V
PWM 3L – 3.4V | PWM 3L – 6.2V

In the beginning of this project, this part of the subsystem was tested by connecting the PWM inputs to the development board and obtaining the 3.3V and 5V Vcc voltages for the isolators from a power supply. When full system testing was completed, these values were obtained by connecting the PWM input wires to the MCU, and the 3.3V and 5V Vcc voltages were obtained from the power and MCU subsystems via auxiliary power.

In addition to the correct values being output, the speed of these PWMs responded to the speed knob or potentiometer spinning. The speed knob functionality is essential to the controllability of the motor, and since the output of the PWM isolation worked with the speed knob, the PWM isolation was fully functional.

Another portion of the digital isolation was the relay control. On the optoelectronics board, this included a signal of 3.3V input when the motor was on and 0V when the motor was off. This on and off functionality was realized by a button on the MCU board. In Figures 8, 9, and 10, it is shown that when the button is pressed on the input voltage is 3.3V and output is 5V, and when the button is off, the output voltage was 0V.

Table 1: PWM Input and Output Isolation Voltages

Subsystem Report | Revision - 1

Figure 8: Relay Isolation Input Button On (3.4V)

Figure 9: Relay Isolation Output Button On (5.8V)

Subsystem Report | Revision - 1

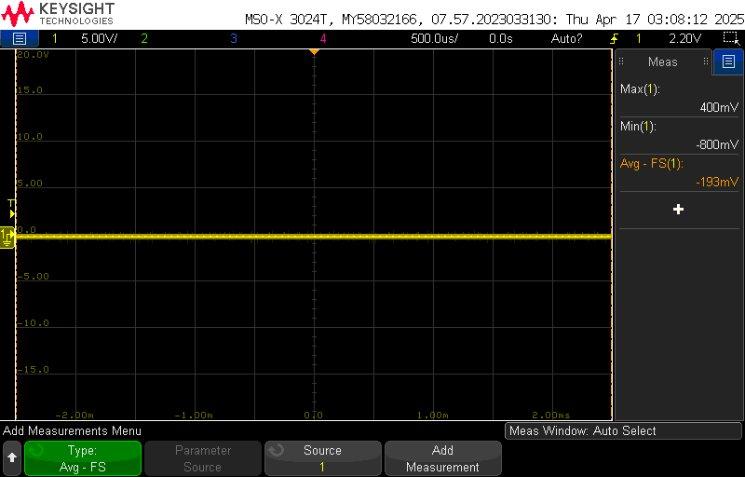
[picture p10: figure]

Figure 10: Relay Isolation Output Button Off (~0V)

An interesting mistake that was made in this portion of the optoelectronics board was the 3.3V Vcc for the isolators. The power to digital side requires 3.3V for the diodes, so 3.3V is on two connectors. Upon close inspection, the 3.3V Vcc was not actually routed to the 3.3V on the connector, but the circuit was working for a good amount of time when it appears that 3.3V was never connected, so it never should have been working. The isolators did end up stopping working which is what inspired the trace inspection. It was a very easy fix, just adding a thin blue wire, as seen in Figure 3 above, to connect 3.3V to the traces with the isolators. It is a mystery that has still not been solved, but now the circuit works because the error has been corrected.

### 2.3.2. Power to Digital Isolation Validation

This part of the subsystem proved to be much more difficult to test and validate than the PWM and relay isolation. This portion of the optoelectronics subsystem was never fully tested and validated. In the beginning of the project, the tests that were thought to be correct and proof of the circuitry working were not correct. The Vcc and GND as mentioned earlier were switched on all nine op-amps for this side of the board, so the op-amps never turned on which means the isolators did not get the correct voltages, so the whole test was inaccurate. This issue was first discovered when connecting auxiliary power, which was mentioned earlier.

Subsystem Report | Revision - 1

The other subsystems were able to successfully create 15V from the 120VAC wall voltage, and when it was plugged into this board, the voltage dropped from 15V to around 4V. After cutting and replacing the incorrect traces to fix the problem, the voltage drop was gone. In Figure 11 below, the lack of voltage drop can be seen, as the DC power supply is set to supply 15V and it is.

Figure 11: 15V Supply Voltage Showing No Drop

Once this issue was solved, it was time to actually test. The requirements state that at full power, 120VAC, around 60V should be input from the power control and 15V should be output to the MCU. This requirement was for each of the three circuits: voltage, current, and temperature feedback. Because the 120VAC is a pretty dangerous voltage, it was advised to wait until the last moment to plug the system into the wall. To test this part of the subsystem, without having the full power feedback values, 15V input voltage was applied, and the values were as follows:

Feedback Signal | Input Voltage | Output Voltage
bus.v | 15 V | 3.9 V
ilim.v | 15 V | 3.9 V
ips.temp | 15 V | 3.9 V
Table 2: Diagnostic Feedback Input and Output Voltages

Subsystem Report | Revision - 1

Based on this nomenclature, bus.v is the voltage that the motor is running at, ilim.v is the current, and ips.temp is the temperature. Based on the ratio, 15V:3.9V simplifies to 1V:0.26V. Had the full 60V been input, based on the ratio, ~15.6V would have been output. This voltage is within the 15-20V threshold in the requirement, so it is reasonable to assume this circuitry would work and be accurate at full power.

### 2.4. Subsystem Conclusion

Overall, this subsystem worked as expected, and it performed correctly when connected to the other subsystems to form the full system. The PWM isolation circuit works well and is an important part of spinning the motor. The PWMs are input from the MCU at 3.4V and output to the power control at 6.2V and 6.0V. This isolation helps the MCU to not come in contact with the high voltage of the motor and power electronics, and the increase in voltage allows the PWMs to be large enough to be taken in by the power control. The relay or on/off signal also works correctly, where before isolation there is 3.4V when the button is on before the isolators and 5.8V after. When the button is off, the relay signal is 0V before and after isolation. The power to digital isolation which is used for the diagnostic feedback also works as expected. This part was never fully tested due to timing, however. The motor spinning was the main focus of the team, so the feedback section was second priority. The optoelectronics section of feedback worked, but there were other problems with integration that could have been solved had there been a few more weeks. The validation of this part of the optoelectronics subsystem seemed to be correct, so in theory, it should have worked correctly at full power.

Subsystem Report | Revision - 1

## 3. Microcontroller Subsystem Report

### 3.1. Subsystem Introduction

This subsystem refers to the hardware of the microcontroller portion of the VFD motor controller. In order for the firmware to control the motor, the microcontroller must be implemented properly. This subsystem is powered by two of the three phase AC power supply which is sent to the MCU for functionality.

### 3.2. Subsystem Details

The DSPIC33CK256MP508 microcontroller was selected for this project. It has an adequate amount of analog and digital pins to support the VFD motor and the required PWM signals necessary. This MCU has 80 pins however only 32 are needed for this application. The MCU is supplied by the 15 VDC from the AC power supply fed by the main power. The voltage will then be stepped down to a usable 3.3V using a 3.3V fixed buck converter. The buck converter takes the 15V from the AC/DC converter to a usable voltage for the microcontroller. This 3.3V is needed for the microcontroller along with the Pickit4 debugger and the UART serial interfaces.

The MCU subsystem receives feedback through low-voltage analog signals representing voltage and current. The MCU then sends out PWM signals to the H bridge and power control system which are used to control the inverter stage of the VFD which helps to adjust the output voltage and frequency supplied to the motor.

The hardware necessary for the application is placed onto a PCB and the firmware will be coded onto the MCU to control the PWM signals. A potentiometer is included to vary the frequency of these PWM signals. A push button will also be used to turn the motor on and off which is indicated by a green LED. A 5 pin connector is used to connect to the Pickit5 debugger which is used to flash the code onto the MCU. A 3 pin connector is used for UART serial communication using a cable to connect to a PC. Finally, a 20 pin connector is used to

Subsystem Report | Revision - 1

send the PWM signals back to the H bridge and to connect to the GPIO pins. This PCB will later be connected to the power and optoelectronics subsystems.

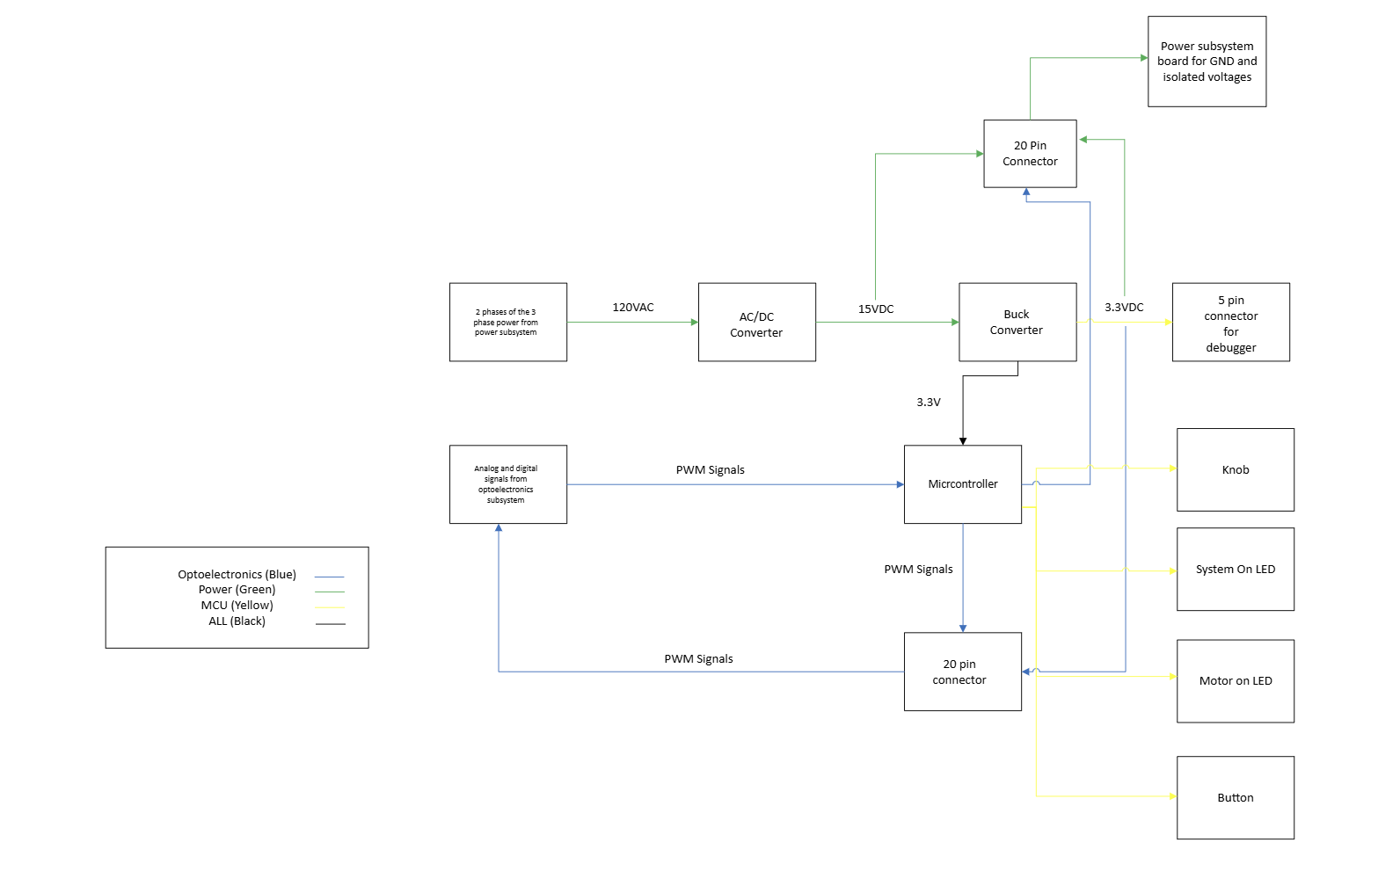
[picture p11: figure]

Pin | Function
1 PWM1H
2 GPIO
3 PWM1L
4 GPIO
9 MCLR
11,32,50,70 | VSS
12,31,51,71 | VDD
17,22,39,44 | GPIO
19 GPIO (Potentiometer)
24 GPIO (LED 2)
25 AVDD
26 AVss
34 Clock input
37 GPIO (LED 1)
42 GPIO (Relay)

Figure 12: MCU Block Diagram

Subsystem Report | Revision - 1

60 PGD1
61 PGC1
68 UART TX
69 UART RX
75 PWM3H
76 PWM3L
78 PWM2H
80 PWM2L

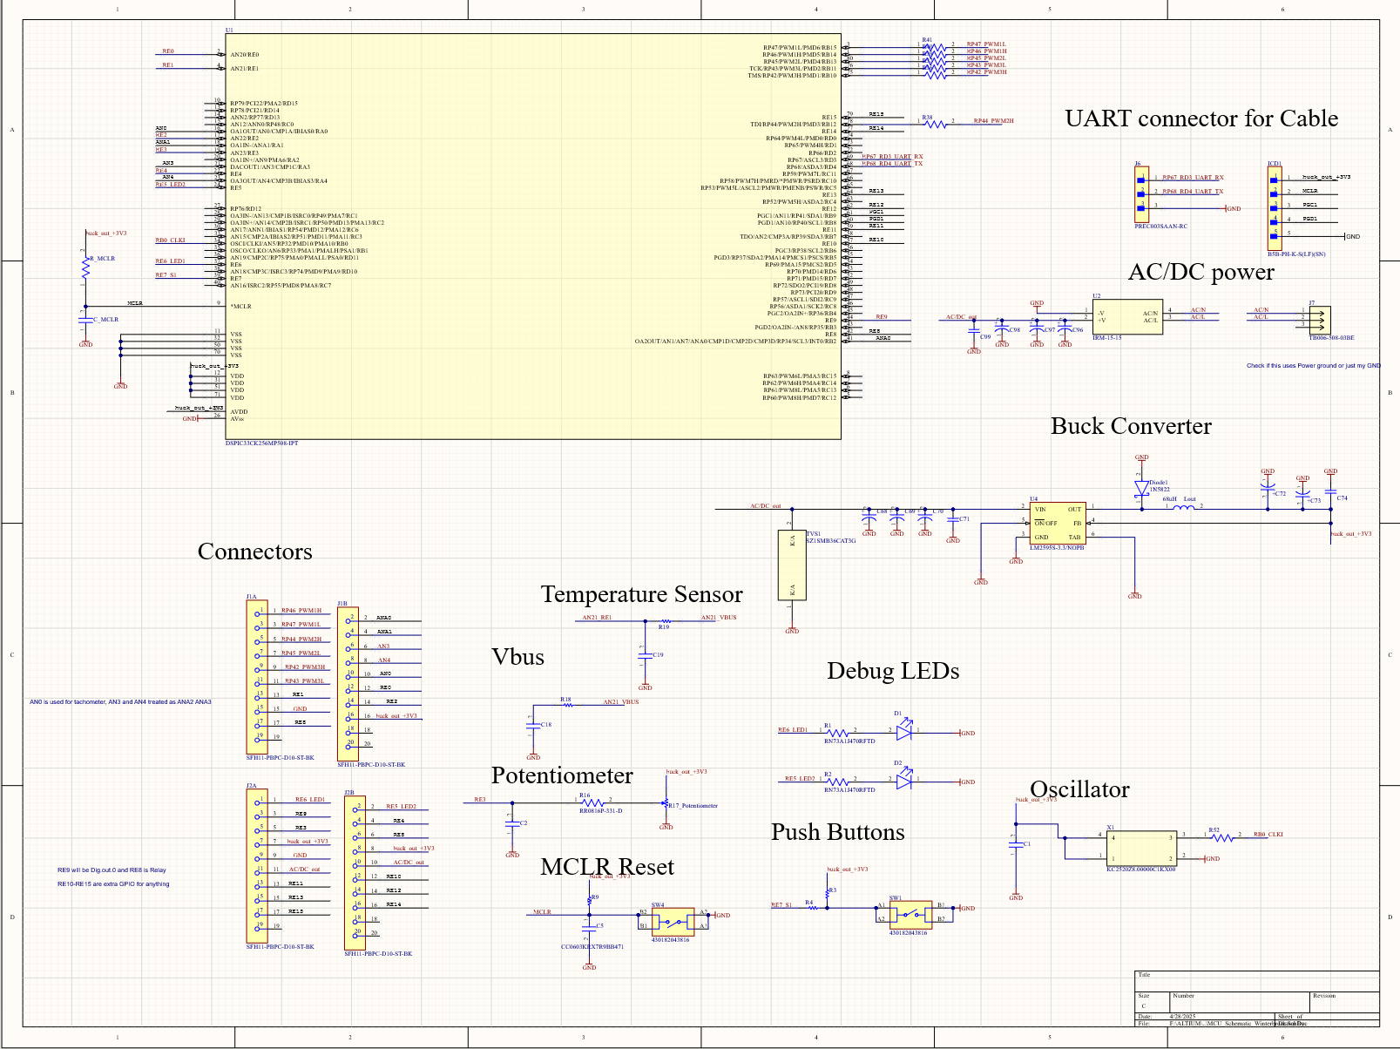
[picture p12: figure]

### 3.3. Subsystem Validation

This subsystem refers to the hardware portion and PCB design for the microcontroller. This includes the 15V AC/DC converter, 3.3V buck converter, MCU, potentiometer, system and motor LEDs, and the on/off button. The IRM-15-15 AC/DC converter will take in the 120VAC wall power from the power subsystem board and convert it to 15VDC. This 15VDC will then be stepped down using the LM2595s-3.3 to convert it to 3.3V in order for the MCU to function.

Table 3: Pin interface for DSPIC33CK256MP508 Microcontroller

Figure 13: MCU subsystem schematic

Subsystem Report | Revision - 1

The MCU will then be coded by the firmware to implement the system and motor LEDs, the potentiometer (knob), the on/off button, and to send out the PWM signals to the optoelectronics board.

### 3.3.1. Converter Validation

The first portion of the subsystem that was tested and validated were the power converters. The 3.3V buck converter was the first converter to be validated. Last semester the schematic and corresponding pcb routing was done incorrectly. For the final revision of the buck converter, different through hole capacitors were added along with a different diode. This converter was tested by injecting a variety of voltages using the DC power supply along with load resistors for the line and load regulation tests. The AC/DC converter was then tested after ensuring that the buck converter functioned properly. This was only tested by using wall power (~120VAC) and plugging it into the board and measuring the output on one of the 20-pin connectors used for supplying the Power subsystem board.

Load (mA) | Vout (V)
0 | 3.2993
30 | 3.2952
50 | 3.2824
72 | 3.2812
95 | 3.2601
122 | 3.2512
153 | 3.2243
Vin (V) | Vout (V)
16.0 | 3.003
15.5 | 3.2997
15.0 | 3.2997
14.5 | 3.2995
Vin (VAC) | Vout (VDC)
118 | 15.0

### 3.3.2. Button and Relay Signal Validation

This portion of validation was done after the board was fully assembled. The button and relay signal was unable to be tested the first semester because the buck converter circuit was

Table 4: Load regulation validation for buck converter (LM2595-3.3s)

Table 5: Line regulation validation for buck converter (LM2595-3.3s)

Table 6: Validation for 15V AC/DC converter (IRM-15-15)

Subsystem Report | Revision - 1

made incorrectly, causing the MCU to not have the proper power. After ensuring the MCU received the proper 3.3V from the buck converter, the code was flashed using a Pickit5 and MPLAB using the 5-pin connector on the board. After this was done, the button was given functionality over the relay signal. The first test done was to ensure the button functioned properly and could turn on and off. The second test ensured the relay was funcitoning properly and was connected to the button.

Button
Not Pressed | Pressed
3.25V | -.048V

Relay
On | Off
3.281V | -.045V

### 3.3.3. LED Validation

After ensuring the button and relay works the LEDs were validated. The original LEDs failed to function properly due to improper soldering, however the component was small and there was a risk of burning a pad when trying to get them off. The addition of two LEDs -- one red and one blue – was done as a compromise. These LEDs were placed in the vias for the original LEDs and blue wired to a GND via. They were positioned to avoid a possible short. The first LED to be tested was the power on LED (red). When the components receive the 3.3V from the buck converter the red LED shall light up as shown below. The blue LED turns on when the button is pressed indicating that the motor is on.

Table 7: Button signal voltage when button is toggled

Table 8: Relay signal voltage when toggled

Subsystem Report | Revision - 1

Figure 14: Power On LED (red)

Figure 15: Motor On LED (blue)

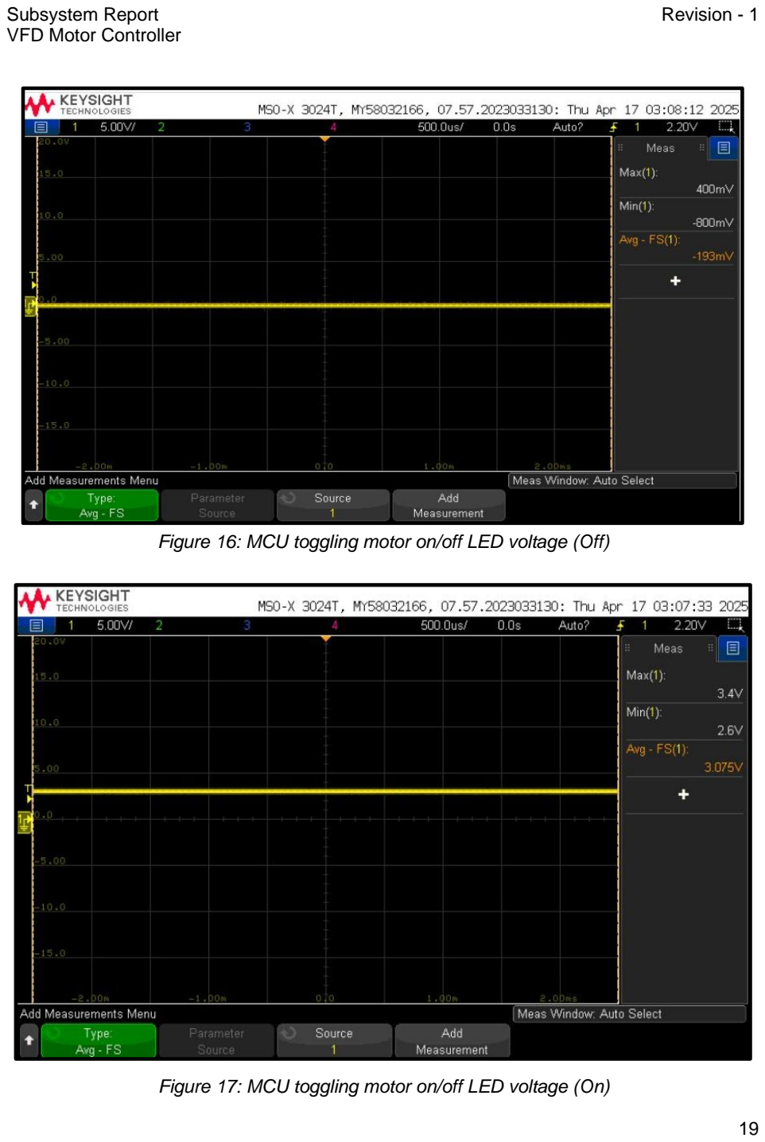
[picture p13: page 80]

Subsystem Report | Revision - 1

Figure 16: MCU toggling motor on/off LED voltage (Off)

Figure 17: MCU toggling motor on/off LED voltage (On)

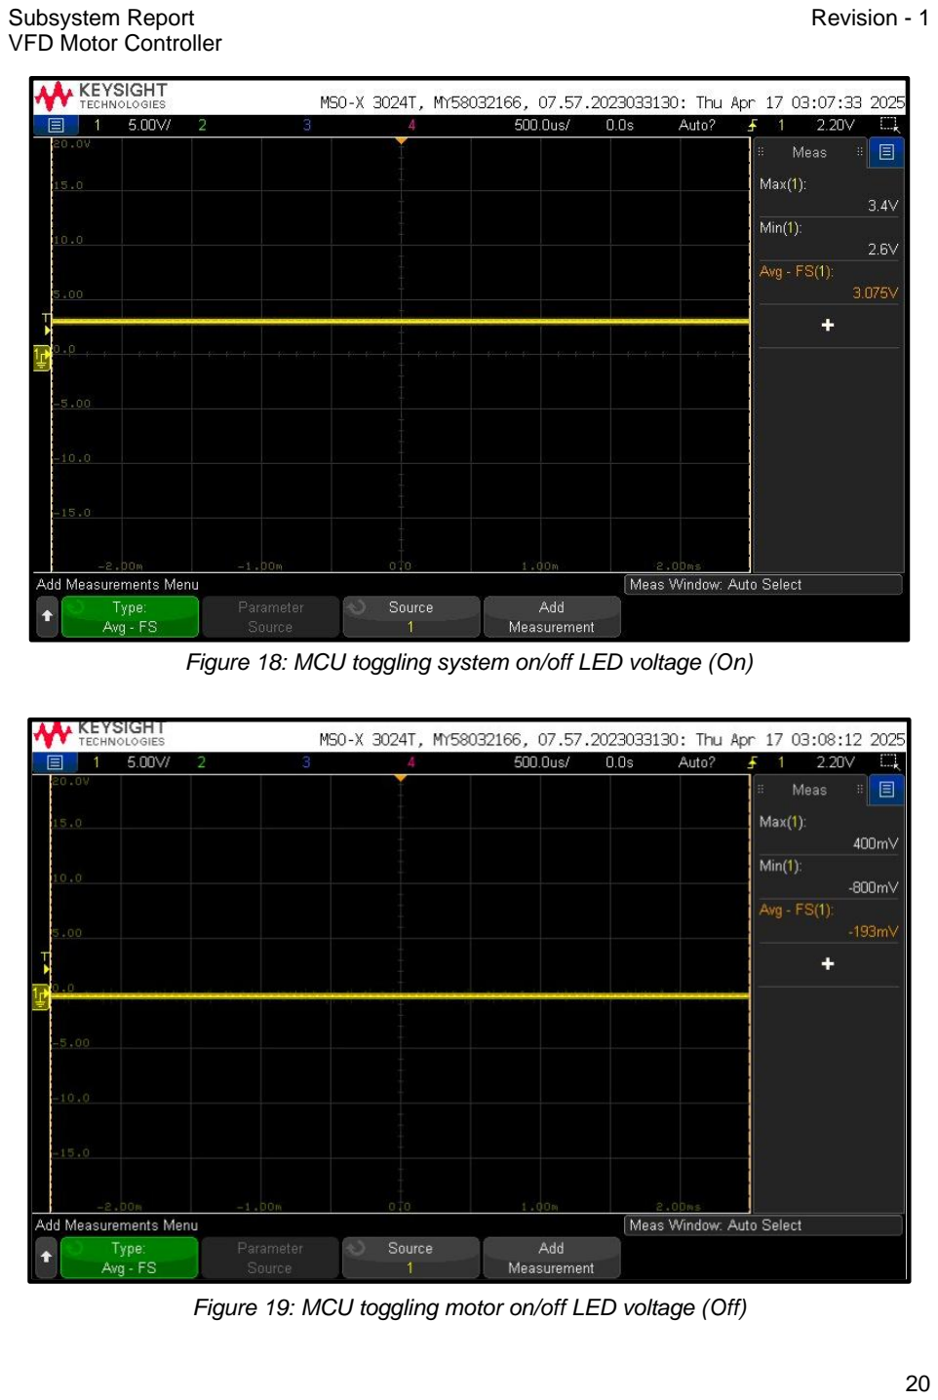
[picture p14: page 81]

Subsystem Report | Revision - 1

Figure 18: MCU toggling system on/off LED voltage (On)

Figure 19: MCU toggling motor on/off LED voltage (Off)

Subsystem Report | Revision - 1

### 3.3.4. Knob and PWM Validation

In order for the motor to function properly, the correct PWM signals need to be produced by the MCU. Three high and three low signals need to be produced, and the knob must be able to change the frequency of these signals. The second revision of the PCB did not have the knob (potentiometer) properly routed. Pin 19 on the MCU was then routed to the potentiometer for it to be coded and function properly.

Figure 20: Three high and three low PWMs with knob signal

Subsystem Report | Revision - 1

Knob
Positions | Voltage
Low | -.045V
Middle | 1.603V
High | 3.285

The lower voltage levels indicates that the motor will be spinning at a lower speed. As the knob is turned counterclockwise, the voltage reaches its maximum (~3.3V) indicating it's at its maximum speed.

Signa l | Frequenc y (kHz) | Minimu m Voltage | Maximu m Voltage | Phase Offset (degrees) | Low Knob Value - Low Frequency | High Knob Value - High Frequency
1H | 1 | -0.13V | 3.65V | 0 | TRUE | TRUE
1L | 1 | -0.13V | 3.65V | 0 | TRUE | TRUE
2H | 1 | -0.13V | 3.65V | 120 | TRUE | TRUE
2L | 1 | -0.13V | 3.65V | 120 | TRUE | TRUE
3H | 1 | -0.13V | 3.65V | 240 | TRUE | TRUE
3L | 1 | -0.13V | 3.65V | 240 | TRUE | TRUE

### 3.4. Subsystem Conclusion

Overall this subsystem functioned properly up until the end. The 15V AC/DC converter brick stopped working after a few full system tests at the end of the semester. The diagnostic feedback was also unable to be coded using the TTL-232R-RPi debug cable and MPLAB. The rest of the functionalities of the MCU worked without fail. After switching from the faulty Pickit4 to the newer Pickit5, the code was easily able to be flashed onto the MCU. It was able to output the proper PWMs for the motor to run and was also able to control the speed using the knob. The start/stop button worked as well and the blue LED was turned on when the button was pressed on. Although the LEDs caused a few hiccups along the way, a compromise was made and the through-hole LEDs functioned as needed. The red system power LED lit up when the board received the proper amount of voltage. With the 15V being injected to the LM2595-3.3s buck converter to bypass the broken 15V AC/DC converter, the full system was able to obtain the needed 3.3V and 15V from this subsystem’s PCB board. The MCU received the proper voltage and a safe amperage level; the power board was able to receive the common GND, and the 15V and 3.3V needed for isolation, and the optoelectronics board was able to receive the PWMs, 3.3V, and common GND from the board. With this shortcut, the full system was able to function properly and the validation indicates the system should work under full power.

Figure 21: Knob position and corresponding voltage level

Figure 22: Knob effect on PWM signals

Subsystem Report | Revision - 1

## 4. Power Subsystem Report

### 4.1. Subsystem Introduction

The power subsystem of the VFD motor controller is responsible for supplying power to both an AC induction motor and the entire system. It is designed to operate with 120 VAC three-phase power and has been tested to ensure safe and reliable performance. The following sections present an analysis of the subsystem's operation and validation.

### 4.2. Subsystem Validation

### 4.2.1. Rectifier and DC Link Validation

A rectifier converts AC to DC, while a DC link filters the output. In Figure 23, the rectifier schematic is shown. First, a power input connector receives the desired three-phase power. Next, a set of capacitors in parallel with varistors is connected across each phase. The capacitors filter the voltage to reduce noise, and the varistors provide protection against voltage surges. Finally, a full-wave rectifier converts the AC to DC.

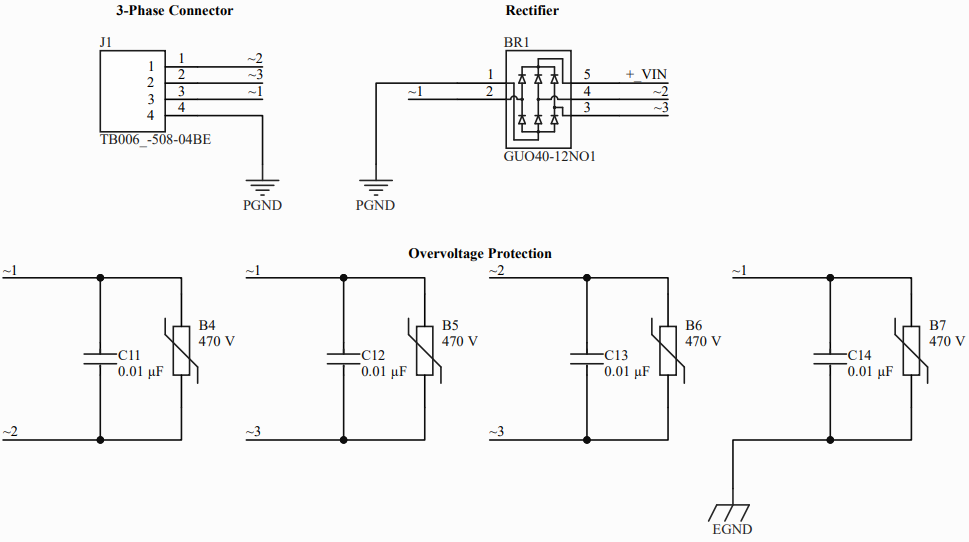
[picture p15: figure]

Figure 23: Rectifier Schematic

Subsystem Report | Revision - 1

In Figure 24, the DC link schematic is shown. First, a fuse provides protection against overcurrent. Next, a varistor in parallel with a set of capacitors is connected to ground. The varistor provides protection against voltage surges, and the capacitors filter the voltage to reduce noise.

The rectifier and DC link were validated by supplying an input AC voltage and measuring the output DC voltage, as shown in Figure 25. While the integrated system is designed to operate at 120 VAC, the validation testing was conducted at 10 VAC. The three-phase AC was generated using three waveform generators, with phase A and phase B values in Figure 26 and phase C values in Figure 27. An amplitude of 3.536 Vrms was used to produce the desired voltage. Additionally, each phase was offset by 120˚ to simulate a three-phase system, with phase C further adjusted due to the waveform generators not being synchronized.

Figure 24: DC Link Schematic

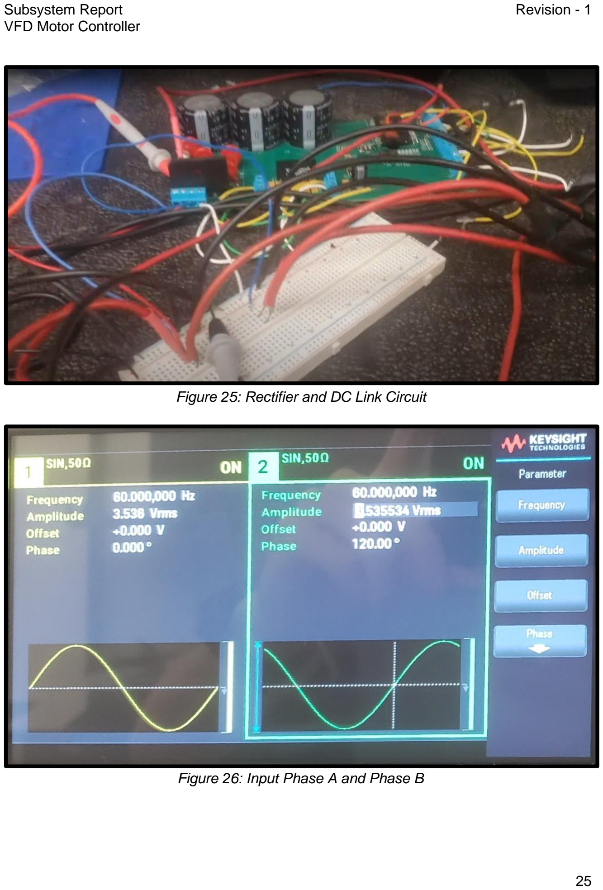
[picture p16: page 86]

Subsystem Report | Revision - 1

Figure 25: Rectifier and DC Link Circuit

Figure 26: Input Phase A and Phase B

Subsystem Report | Revision - 1

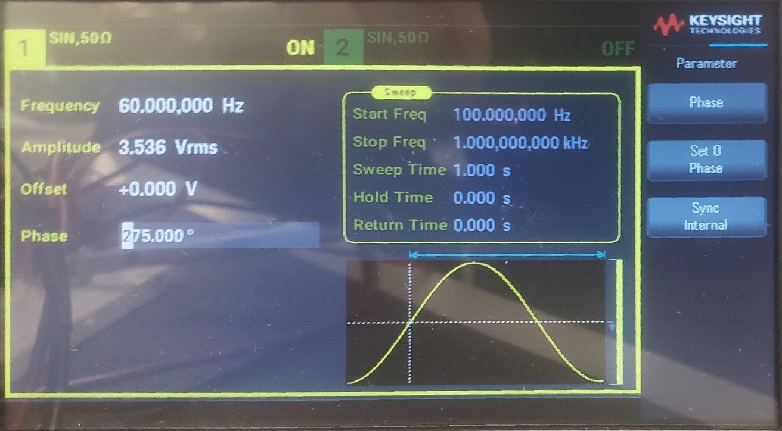
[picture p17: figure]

Upon measuring the input AC waveforms shown in Figure 28, the green (phase A), blue (phase B), and purple (phase C) sinusoidal waves demonstrate a phase shift of 120 degrees and an amplitude of 10 VAC. Furthermore, the measured DC output is 9.6 VDC with 600 mV of noise. This differs slightly from the expected output of 12 VDC .This discrepancy can be attributed to the forward voltage drop across the rectifier diodes and losses within the rectifier and DC link circuitry. Despite these factors, the measured value remains within an acceptable range for the system's operation.

Figure 27: Input Phase C

Subsystem Report | Revision - 1

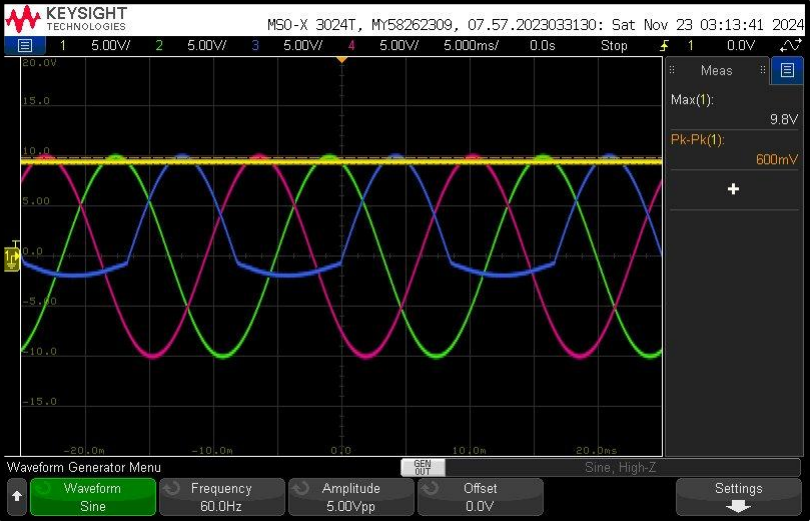
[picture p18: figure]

### 4.2.2. Power Control Validation

The power control takes an input of DC voltage from the DC Link and based on the input PWM signals from the microcontroller, inverts the DC voltage into the appropriate AC voltage to power the motor. The power control was validated by applying an input DC voltage and PWM signals and measuring the output waveforms. In Figure 29, the measured output waveforms are shown to be the expected modified sine waves at 120 degree phase shift. Furthermore, the input dc voltage was generated using a DC power supply and the PWM signals were generated using the integrated system.

Figure 28: Input Phase A, Phase B, Phase C; Output DC

Subsystem Report | Revision - 1

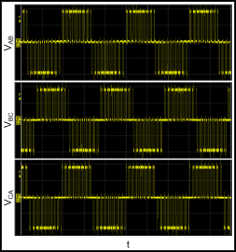
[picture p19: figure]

4.2.3. 3.3 VDC to Isolated 5 VDC Converter Validation

The 3.3 VDC to isolated 5 VDC converter converts 3.3 VDC to isolated 5 VDC. In Figure 30, the 3.3V/ISO_5V converter schematic is shown. First, an input connector receives the input 3.3 VDC. Next, a set of capacitors in parallel is connected to ground, to filter the voltage and reduce noise. Then, a power converter steps up and isolates the 3.3 VDC to 5 VDC. Finally, another set of capacitors in parallel is connected to ground, to filter the voltage and reduce noise.

Figure 29: Power Control Output

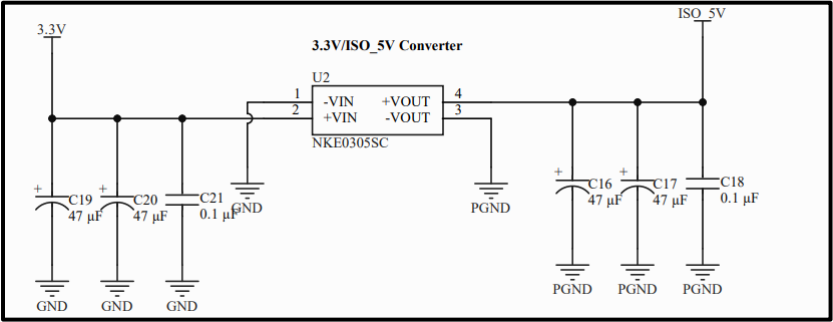
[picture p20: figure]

Figure 30: 3.3V/ISO_5V Converter Schematic

Subsystem Report | Revision - 1

The 3.3 VDC to isolated 5 VDC converter was validated by supplying an input voltage and measuring the output voltage under varying loads. The validation testing was conducted at an input voltage of 3.3 VDC using a DC power supply and the varying currents using an electronic load. The resulting data was recorded in Table 9.

Iout (mA) | Vout (V)
12 | 5.381
50 | 5.188
100 | 4.981
150 | 4.782
200 | 4.581

Furthermore, the 3.3 VDC to isolated 5 VDC converter was validated by supplying various input voltages and measuring the output voltage. The validation testing was conducted at a range of values similar to the operating voltage of 3.3 VDC and was generated using a DC power supply. The resulting output voltages were recorded in Table #.

Vin (V) | Vin,pp (mV) | Vout (V) | Vout,pp (mV)
2.8 | 500 | 4.9 | 500
3.2 | 500 | 4.8 | 500
3.3 | 500 | 5.3 | 500
3.6 | 900 | 5.7 | 500

Upon measuring the output voltages in Table 9 and Table 10, the converter behaved as expected for its full range of voltage and current values.

4.2.4. 15 VDC to Isolated 15 VDC Converter Validation

The 15 VDC to isolated 15 VDC converter converts 15 VDC to isolated 15 VDC. In Figure 31, the 15V/ISO_15V converter schematic is shown. First, an input connector receives the input 15 VDC. Next, a set of capacitors in parallel is connected to ground, to filter the voltage and reduce noise. Then, a power converter isolates the 15 VDC to 15 VDC. Finally, another set of capacitors in parallel is connected to ground, to filter the voltage and reduce noise.

Table 9: 3.3V/ISO_5V Converter Load Regulation Test

Table 10: 3.3V/ISO_5V Converter Line Regulation Test

Subsystem Report | Revision - 1

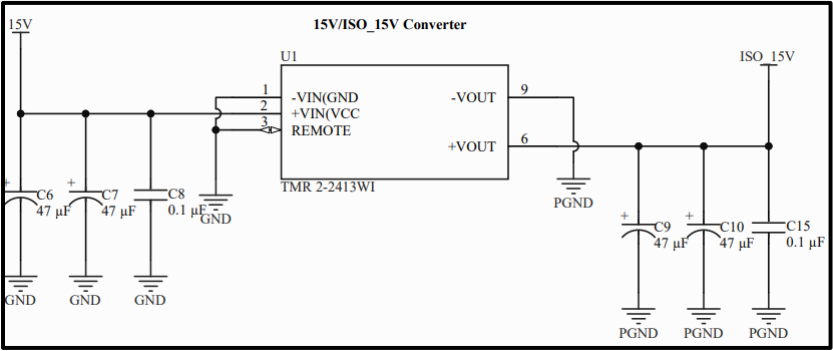
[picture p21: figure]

The 15 VDC to isolated 15 VDC converter was validated by supplying an input voltage and measuring the output voltage under varying loads. The validation testing was conducted at an input voltage of 15 VDC using a DC power supply and the varying currents using an electronic load. The resulting data was recorded in Table 11.

Iout (mA) | Vout (V)
12 | 14.959
25 | 14.951
50 | 14.937
75 | 14.924
100 | 14.912
125 | 14.898
134 | 14.893

Furthermore, the 15 VDC to isolated 15 VDC converter was validated by supplying various input voltages and measuring the output voltage. The validation testing was conducted at a range of values according to the datasheet and was generated using a DC power supply. The resulting output voltages were recorded in Table 12.

Figure 31: 15V/ISO_15V Converter Schematic

Table 11: 15V/ISO_15V Converter Load Regulation Test

Subsystem Report | Revision - 1
Vin (V) | Vin,pp (mV) | Vout (V) | Vout,pp (mV)
9.1 | 200 | 15.1 | 400
15.1 | 500 | 15.0 | 400
20.9 | 500 | 14.9 | 400
27.0 | 500 | 15.3 | 500
33.0 | 578 | 14.9 | 264
35.8 | 503 | 14.9 | 264

Upon measuring the output voltages in Table 11 and Table 12, the converter behaved as expected for its full range of voltage and current values.

### 4.2.5. Relay Validation

The relay takes in the relay signal and toggles the motor power between on and off using a switch. In Figure 32, the schematic is shown. In the left contact position, the DC voltage is input using a DC power supply and in the right contact position the DC voltage will be output if the switch is closed. Next, the coil voltage is set to 15 VDC, but the circuit is incomplete because of the MOSFET position relative to PGND. So, the relay signal of 5 VDC is generated using a DC power supply to trigger the MOSFET, completing the coil voltage to PGND, and the switching the relay closed.

Table 12: 15V/ISO_15V Converter Line Regulation Test

Subsystem Report | Revision - 1

The relay was validated by supplying an input voltage of 15 VDC to the contact and connecting the 15 VDC input to the coil. Next, the 5 VDC relay signal was generated using a DC power supply to close the switch and allow the 5 VDC to pass through the relay as measured in Figure
33. Then, the simulated relay signal was disconnected to open the switch and stop the 5 VDC to pass through the relay as measured in Figure 34.

Figure 32: Relay Schematic

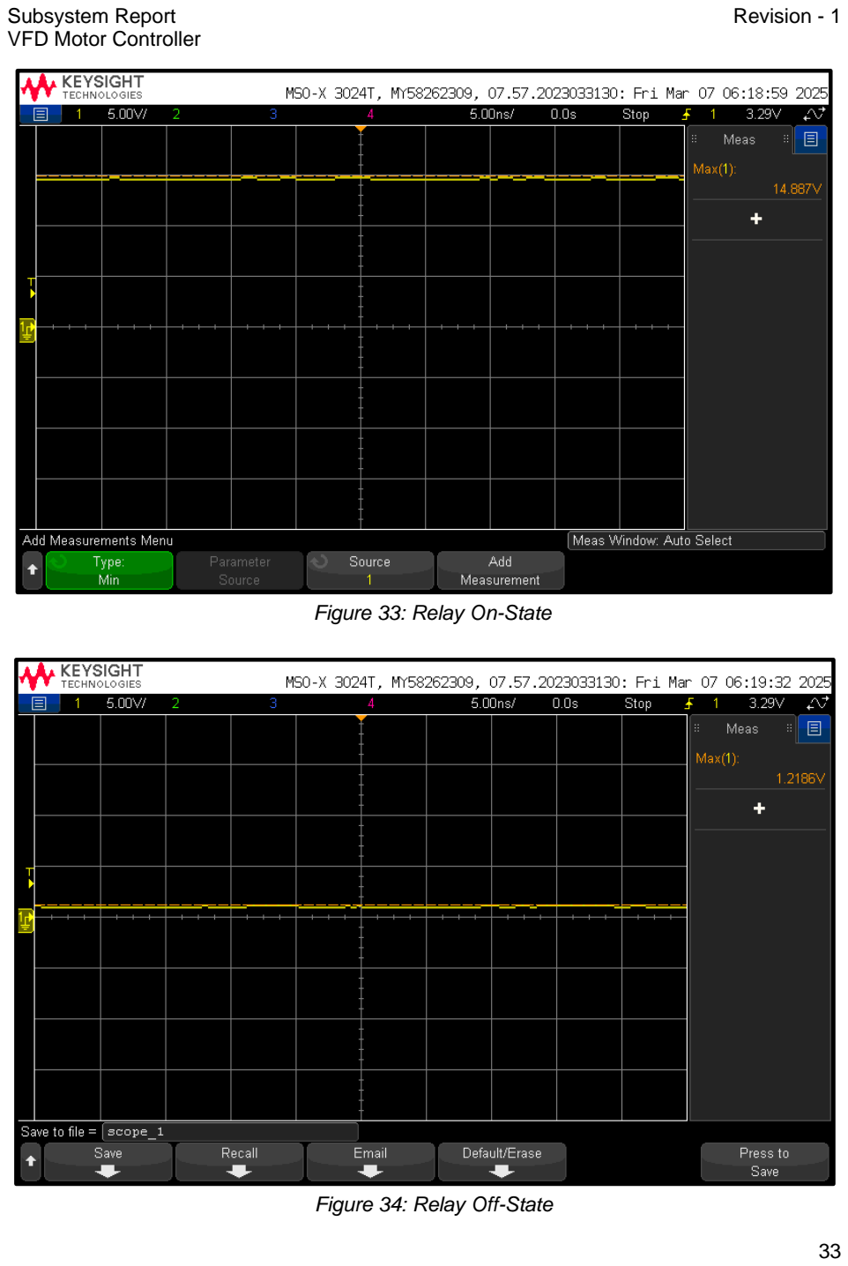
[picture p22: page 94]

Subsystem Report | Revision - 1

Figure 33: Relay On-State

Figure 34: Relay Off-State

Subsystem Report | Revision - 1

Upon measuring the output voltages in Figure 33, the yellow horizontal line shows approximately 15 VDC. Upon measuring the output voltages in Figure 34, the yellow horizontal line shows approximately 1.2 VDC. This aligns greatly with the expected change of 15 VDC when toggling the relay. Any remaining voltage difference to zero, likely due to noise and measurement inadequacies.

### 4.2.6. Diagnostic Feedback Validation

The diagnostic feedback was designed to output the measurement signals of voltage, current, and temperature from the power control only when the full system is functioning. The voltage measurement came from the DC bus voltage after it has experienced voltage drop due to resistors. Due to this, low voltage testing resulted in an output value of zero because the DC bus voltage was not high enough. The current measurement came as a voltage from the power control into a current sensor designed to sense 30 A. Since this system was designed for 2 A, the voltage from the power control was not high enough and the current sensor resulted in an output value of zero. The temperature measurement came a power control pin and would have resulted in a voltage identifying the power control as overheating. Because the diagnostic feedback was pushed back to the end of the project and the full 120 VAC was only utilized at demo, this portion of the project fell out of the completed scope.

### 4.3. Subsystem Conclusion

In conclusion the rectifier, DC link, power control, 3.3 VDC to isolated 5 VDC converter, 15 VDC to isolated 15 VDC converter, and relay were all working properly. On the other hand, the diagnostic feedback was not working properly. With a few more weeks the diagnostic feedback portion could have been adapted to the final project design, integrated with the rest of the project, and communicated the voltage, current, and temperature to the user via a monitor. Ultimately, the power subsystem succeeded in its objective to take in 120 VAC, rectifier it to DC, invert it back to AC, and run the motor. It also succeeded in distributing auxiliary power, switching the motor on and off, and changing the motor speed in response to PWM signals.

Subsystem Report | Revision - 1

## 5. Firmware Subsystem Report

### 5.1. Subsystem Introduction

This subsystem entails all programming required to make the microcontroller work. Without the microcontroller and its firmware, the remaining VFD subsystems could not function together to control the motor. The firmware is also responsible for presenting the user with an interface that allows direct control of the VFD’s start/stop functionality, and PWM frequency (motor speed).

### 5.2. Subsystem Details

The firmware was all written, tested, and demonstrated in MPLAB’s X IDE in the C language using a DSPIC33CK256MP508 microcontroller on a dsPIC33CK Curiosity Development Board (part number DM330030). There were three primary objectives of the firmware as part of this system. The first being to output a three phase PWM signal with adjustable frequencies based on a potentiometer. The second objective is to toggle a relay signal when a button is pressed on the microcontroller’s PCB. Finally, the firmware should take three feedback signals that are input to the microcontroller and output them to the UART console. Two of these three objectives were successfully validated; the group decided to abandon the objective regarding the feedback signals due to problems with the values that they would send, and problems getting print statements to correctly appear in the UART console.

The program works by continuously reading the potentiometer’s value and using that to calculate the desired frequency (10-60Hz) that should be outputted to the motor via the PWM signal. The program generates a table of sine values that are then mapped to duty cycle percentages between 1-100%. It then uses the High Speed PWM (HS PWM) module in MPLAB X IDE to produce 3 1kHz frequency PWM waves at a 120-degree offset (three phase) and their low counterparts. Upon calculating the desired 10-60Hz frequency based on the potentiometer value, the firmware calculates a step increment to determine how fast the PWMs are set to iterate through the sine table, which determines the frequency of these changing waves. This sine wave is the beginning of what the motor will eventually receive as an AC power signal after passing through the other three subsystems.

### 5.3. Subsystem Validation

To validate my subsystem, I tested it on the dsPIC33CK Curiosity Board. I was able to get it to properly display three different phases of a PWM signal iterating through a sine waveform of duty cycles that were all correctly offset by 120 degrees. I was also able to program the complete functionality of the potentiometer so that it can increase and decrease the frequency of the PWM signal. Though the duty cycles of the PWM waves continuously change, the

Subsystem Report | Revision - 1

oscilloscope’s output of these three phases in a single frame of the loop is shown in the figure below. This validation shows that the firmware is ready for subsystem integration next semester.

When the program is running on my development board, it also prints several variables in each iteration of the while loop to a terminal window that can be opened in MPLAB. The variables output in each iteration are shown in the figure below. These print statements were later found to be slowing down the frequency of output PWM waves. Upon deleting the print statements, the correct frequencies were output. It is worth noting that this problem can also be solved by changing the frequencies of the PWM waves inside a timer interrupt and keeping the print statements in the main while loop; however, when this change was made, the motor did not run for an unknown reason.

Tables 7-8 and Figures 14-22 (in the microcontroller subsystem report) additionally show the correct firmware validation with the microcontroller of the start/stop button (relay signal) and PWM signals.

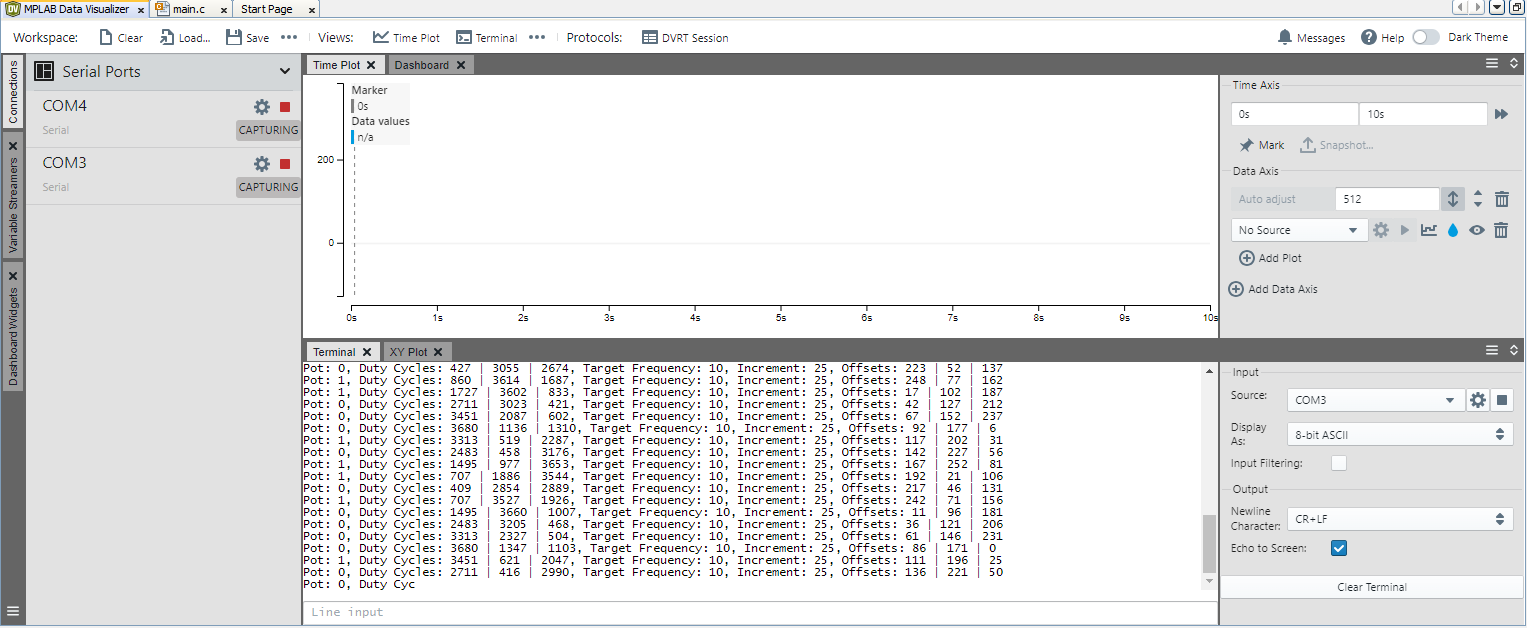
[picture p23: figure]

### 5.4. Subsystem Conclusion

All of my objectives for this project were complete or decided to be left incomplete. The motor was able to run in the end, meaning a successful complete integration between the four subsystems.
In the end, there were still a couple of problems left on the table to solve that could improve the VFD. First, the problem with the motor not turning when the PWMs are modified within a timer interrupt would need to be fixed to use print statements without messing up the PWM frequencies. Then, the problem with the microcontroller’s communication with the UART console would need to be fixed to print any feedback signals. Lastly, there could be additional

Figure 35: Debug Print Statements (Potentiometer at 0)

Subsystem Report | Revision - 1

control added to the button that changes the direction of the motor. This would be done by swapping two of the PWM’s phases upon a certain duration press of the button or pressing the button a certain number of times in-sequence.

Overall, the firmware subsystem is validated, integrated, and – with the use of several solutions to issues that were found and documented throughout each presentation throughout the semester, provides a strong foundation for the future improvement of the programming of the VFD system.

# VFD Motor Controller

# Mackenzie Miller Andrew Nguyen Aidan Rader Ryan Regan

# FINAL SYSTEM REPORT

### REVISION – 0 28 April 2025

### FINAL SYSTEM REPORT

### FOR

## VFD Motor Controller

PREPARED BY:

_____________________________
Author | Date

APPROVED BY:

_____________________________
Project Leader | Date

_____________________________
John Lusher II, P.E. | Date

_____________________________
T/A | Date

Final System Report | Revision - 0

II

### Change Record

Rev. | Date | Originator | Approvals | Description
0 | 04/28/2025 | VFD Motor Controller Team | | Draft Release

Final System Report | Revision - 0

III

Table of Contents | Error! Bookmark not defined.
List of Tables | Error! Bookmark not defined.
No table of figures entries found | Error! Bookmark not defined.
List of Figures | Error! Bookmark not defined.
No table of figures entries found | Error! Bookmark not defined.
1. System Introduction | Error! Bookmark not defined.
1.1. Block Diagram | Error! Bookmark not defined.
2. Integration | Error! Bookmark not defined.
2.1. Auxiliary Power Integration | Error! Bookmark not defined.
2.2. PWM Integration | Error! Bookmark not defined.
2.3. Relay Integration | Error! Bookmark not defined.
2.4. Diagnostic Feedback Integration | Error! Bookmark not defined.
3. System Conclusion | Error! Bookmark not defined.

Final System Report | Revision - 0

IV

### Table of Contents

Final System Report | Revision - 0

V

Final System Report | Revision - 0

VI

### List of Figures

No table of figures entries found.

Final System Report

Revision - 0
VFD Motor Controller

## 1. System Introduction

Our team was tasked with developing a Variable Frequency Drive (VFD). Most of the traditional motor control methods are inefficient and can lead to unnecessary energy consumption and wear on equipment. The aim of a VFD is to solve this problem by more precisely adjusting motor speed with frequency and voltage control, which helps to extend equipment lifespan and optimize performance.
Some key engineering challenges in our project include designing an efficient power conversion system, generating accurate three-phase pulse-width modulation (PWM) signals, and ensuring smooth integration with industrial applications. This project will help our sponsor and any other users to lower operational costs, enhance process control, and promote more sustainable energy use.

### 1.1. Block Diagram

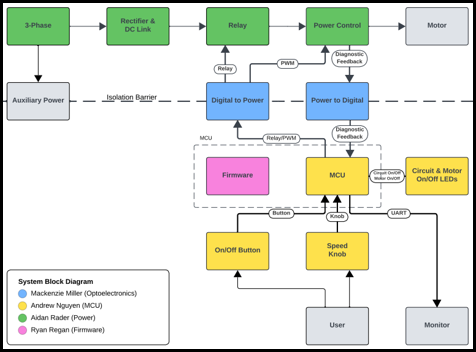
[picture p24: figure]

Figure 1: VFD Motor Controller Block Diagram

Final System Report | Revision - 0

## 2. Integration

### 2.1. Auxiliary Power Integration

Auxiliary power integration includes taking 120VAC into the system from the wall, and transforming it to 15V, Iso15V, 3,3V, and Iso5V.The purpose of the Iso15V and Iso5V is to preserve the isolation barrier, where these two voltages have a different ground than the non-isolated voltages. Auxiliary power serves to create the voltages needed to power all of the components in the system. During integration of this part of the system, there were several challenges to overcome. The two main issues were component failure and testing errors. The 120VAC to 15V converter stopped working unknowingly sometime before the final demonstration. This component was not needed for testing at low voltage without the wall power, so when it came time to plug the system into the wall, this converter did not work. The converter was bypassed during the demo by applying 15V from a power supply to the output of the converter, and this showed that the auxiliary power worked for the rest of the system. Testing precautions were very important in testing the auxiliary power integration due to the high voltage coming from the wall. This made maintaining the isolation barrier and not mixing the grounds extremely important. During testing at one point, an oscilloscope probe was placed to measure the circuit which broke the isolation barrier. This broke the rectifier and exploded a trace out of the power electronics board. If the 120VAC to 15V converter had been replaced, the auxiliary power integration would have been a total success. Since this is a minor issue and was validated before breaking, auxiliary power was a success.

☐ 15 VDC to isolated 15 VDC Conversion

The 15 VDC to isolated 15 VDC converter takes 15 VDC and outputs 15 VDC. Parallel capacitors to the ground are used to filter and smooth the input and output voltages.

☐ 15 VDC to 3.3 VDC Conversion

The 15 VDC is sent to the 3.3 VDC buck converter and outputs 3.3 VDC. Parallel capacitors to the ground are used to filter and smooth the input and output voltages.

☐ 3.3 VDC to Isolated 5 VDC Conversion

The 3.3 VDC to isolated 5 VDC converter takes 3.3 VDC and outputs 5 VDC. Parallel capacitors to ground are used to filter and smooth the input and output voltages.

☐ 120 VAC to 15 VDC Conversion

The 120 VAC from the wall outlet is taken in by the 15V AC/DC converter and outputs 15 VDC. Parallel capacitors to the ground are used to filter and smooth the input and output voltages.

Final System Report | Revision - 0

☐ System On/Off Button
An LED is connected to the MCU to indicate whether the system is on or off. The red through-hole LED will light up indicating the system is powered on and turn off when the system is not receiving power.

### 2.2. PWM Integration

PWM Integration consists of six pulse width modules (PWMs) that were created in the firmware, Figure 2, and flashed onto the microcontroller (MCU) being output at 3.3V, 120 degrees apart and input to the optoelectronics (opto) board where they are transported to the power electronics across an isolation barrier and brought to 5V. These 5V PWMs are then input into the power control where they are transformed into modified sine waves that spin the motor.

This integration happened in multiple steps. The first step was firmware on the development (dev) board connected to the optoelectronics board. The purpose of this was to test the isolation and voltage increase of the optoelectronics board while the MCU board was still in progress. Once the output of the opto board was validated with the dev board, the MCU was added to the integration. The firmware was flashed onto the DSPICK33 using a PICkit 5. A PICkit 4 was originally used, but for some reason the code flashing was unsuccessful. Once the output PWMs of the MCU were validated, as seen in Figure 3, six PWMs, three phases high and low, at 3.4V, the opto board was connected. The input PWMs for isolation were the same PWMs being output of the MCU, and the output PWMs can be seen in Figure 4, the same PWMs as the input, just at 6.0V and 6.2V. After this was validated, the power control was connected, and the output was observed to be a modified sine wave as seen in Figure
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

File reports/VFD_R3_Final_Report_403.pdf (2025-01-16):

# VFD Motor Control

# Mackenzie Miller Andrew Nguyen Aidan Rader Ryan Regan

# CONCEPT OF OPERATIONS

### REVISION – 0 15 September 2024

### CONCEPT OF OPERATIONS

### FOR

## VFD Motor Controller

TEAM VFD MOTOR CONTROL

APPROVED BY:

_____________________________
Project Leader | Date

_____________________________
Prof. Kalafatis | Date

_____________________________
T/A | Date

Concept of Operations | Revision 0
VFD Motor Control

II

### Change Record

Rev. | Date | Originator | Approvals | Description
0 | 9/15/2024 | VFD Motor Control Team | | Draft Release

Concept of Operations | Revision 0

III

### Table of Contents

Table of Contents | III
List of Figures | IV

Concept of Operations | Revision 0

IV

### List of Figures

Figure 1: VFD Motor Control Block Diagram | 2

Concept of Operations | Revision 0

## 1. Executive Summary

The sponsor for this project is in need of a VFD motor controller for an AC induction motor. The VFD will control the speed and torque of the AC motor. This project will help to increase energy efficiency by ensuring that the motor isn’t running at a higher speed than necessary. It also makes the system more reliable and sustainable by decreasing mechanical stress.

A Variable Frequency Drive (VFD) is a device that controls the speed of an electric motor by varying the frequency of the delivered voltage. VFDs are useful because they improve the energy efficiency, reliability, safety, stability, and controllability of a motor. The goal of this project is to make a VFD motor controller that will efficiently control the seed and torque of an electric motor.

Concept of Operations | Revision 0

## 2. Introduction

### 2.1 Background

VFD motor controllers have several beneficial functionalities that can improve the quality of a system. A VFD motor controller regulates the speed and torque of electric motors by controlling the frequency and voltage supplied. The speed is controlled by varying the frequency of the supply of electricity. It also allows for more efficient systems. By running at certain speeds, the VFD can reduce the power consumed, allowing for energy to be saved. It also reduces stress on the motor by allowing for soft starting and stopping. The VFD also has a functionality allowing it to shut off the motor if something is shorted, overheating, or overloaded. The VFD will replace a fixed speed motor in a mechanical system.

### 2.2 Overview

While fixed speed motor controllers are still useful in some applications, more often than not a VFD motor controller is a better alternative. It offers all the functionality of a fixed speed motor controller while also being able to vary the speed and torque of the motor if needed. In this project, our team will work to create a Variable Frequency Drive to control motor speed. In addition, we will consider several different factors such as user interface for the drive, and implementation of the drive in a closed and open loop. This upgrade will improve the energy efficiency, reliability, safety, stability, and controllability of the motor.
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

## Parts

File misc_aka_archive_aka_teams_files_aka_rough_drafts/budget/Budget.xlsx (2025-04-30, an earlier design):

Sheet: Current Order
Part Number | Name | Order # | Item # | Notes | Quantity | $/unit | Actual ($) | Receipt | Vendor Link | Delivery Date | Subsystem | Block Diagram
After Current Order |  |  |  |  |  |  | 1244.59
Before Current Order |  |  |  |  |  |  | 1244.59
Current Order |  |  |  |  |  |  | 0.00

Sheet: Part Recovery
Component | Quantity | Member
B5B-PH-K-S | 13 | Drew
ERJ-3EKF1001V | 11 | Drew
GRM155R71C104KA88D | 12 | Drew
1N5822 | 4 | Drew
CRCW060310K0FKEC | 9 | Drew
KC2520Z8.00000C1KX00 | 1 | Drew
GRM31CC80E227ME11L | 7 | Drew
MH1608-601Y | 9 | Drew
ERJ-U03F1002V | 7 | Drew
RR0816P-331-D | 4 | Drew
Pickit5 | 1 | Drew
C0805C101K5GACTU | 20 | Mackenzie
08051C104K4T2A | 24 | Mackenzie
293D106X9010B2TE3 | 24 | Mackenzie
KSP2907ACTA | 4 | Mackenzie
CRCW080580K6FKEA | 28 | Mackenzie
RC0805FR-071KL | 30 | Mackenzie
CRCW080510K0FKEA | 10 | Mackenzie
CRCW080549R9FKEA | 20 | Mackenzie
CRCW1206300RFKEA | 10 | Mackenzie
LM358AN/NOPB | 1 | Mackenzie
DM330030 | 2 | Ryan

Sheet: Order History Summary
Order # | Notes | Actual ($) | Receipt(s) |  |  | Order Date | Delivery date | Buyer
Before Current Order |  | 1244.59
1 |  | 381.41 | amazon | digikey | mouser | 2024-10-16 | 2024-10-22 | Ryan
2 |  | 332.01 | digikey | mouser |  | 2024-11-06 | 2024-11-13 | Aidan
3 |  | 9.70 | digikey |  |  | 2024-11-13 | 2024-11-18 | Drew
4 |  | 120.75 | mouser |  |  | 2025-02-11 | 2025-02-12 | Mackenzie
5 |  | 31.27 | mouser |  |  | 2025-02-24 | 2025-02-25 | Aidan
6 |  | 62.28 | mouser |  |  | 2025-03-20 | 2025-03-21 | Aidan
7 |  | 91.08 | digikey | mouser |  | 2025-04-03 | 2025-04-07 | Aidan
8 | personal order ($23.22) | 0.00 | n/a |  |  | 2025-04-21 | 2025-04-22 | Aidan
pcb1 | personal order ($35.26) | 0.00 | n/a |  |  | 2024-11-12 | 2024-11-18 | Drew
pcb2 |  | 29.58 | jclpcb |  |  | 2024-11-06 | 2024-11-11 | Mackenzie
pcb3 |  | 63.34 | pcbway |  |  | 2024-11-07 | 2024-11-11 | Aidan
pcb4 | personal order ($44.68) | 0.00 | n/a |  |  | 2025-02-02 | 2025-02-07 | Drew
pcb5 |  | 27.40 | jclpcb |  |  | 2025-02-04 | 2025-02-10 | Mackenzie
pcb6 |  | 28.10 | jclpcb |  |  | 2025-02-06 | 2025-02-10 | Aidan

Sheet: Order History
Part # | Name | Parts Recovery | Order # | Item # | Notes | Quantity | $/unit | Actual ($) | Receipt | Vendor Link | Delivery Date | Subsystem | Block Diagram
W202503250403655 | PCBv2 - opto | Recovered | pcb8 | 1 |  | 1 | 27.40 | 27.40 | Link | jlcpcb | 2025-03-31 | Mackenzie
W202503250025524 | mcu pcbv2 | Lost | pcb7 | 1 |  | 1 | 40.27 | 40.27 | Link | jlcpcb | 2025-03-31 | Drew
W202502062254478 | power pcbv1 | Recovered | pcb6 | 1 | Rev 1, 6.8in*3.92in, solder mask (both), silkscreen (both), 2 layers | 1 | 28.10 | 28.10 | Link | jlcpcb | 2025-02-10 | Aidan
W202502050109609 | PCBv1 - opto | Recovered | pcb5 | 1 |  | 1 | 27.40 | 27.40 | Link | jlcpcb (https://cart.jlcpcb.com/quote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) | 2025-02-10 | Mackenzie
W202502030552736 | mcu pcbv1 | N/A | pcb4 | 1 | personal order ($44.68) | 1 | 0.00 | 0.00 | n/a | jlcpcb (https://cart.jlcpcb.com/quote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) | 2025-02-07 | Drew
W779366AS1Y3 | power pcbv0 | Recovered | pcb3 | 1 | Rev 0, 7.5inx4in, solder mask (both), silkscreen (both), 2 layers | 1 | 63.34 | 63.34 | Link | pcbway (https://member.pcbway.com/Order/CartList?t=1) | 2024-11-11 | Aidan
W202411060712159 | PCBv0 - opto | Lost | pcb2 | 1 |  | 1 | 29.58 | 29.58 | Link | jlcpcb (https://cart.jlcpcb.com/quote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) | 2024-11-11 | Mackenzie
W202411131051640 | mcu pcbv0 | N/A | pcb1 | 1 | personal order ($35.26) | 1 | 0.00 | 0.00 | n/a | jlcpcb (https://cart.jlcpcb.com/quote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) | 2024-11-18 | Drew
35562987 | mouser shipping | N/A | 8 | 0 | personal order ($23.22), combined with 1.3, 0 left | 1 | 0.00 | 0.00 | n/a | mouser | 2025-04-22
IKCM30F60GDXKMA1 | power control | N/A | 8 | 1 | personal order ($23.22) | 1 | 0.00 | 0.00 | n/a | mouser (https://www.mouser.com/ProductDetail/Infineon-Technologies/IKCM30F60GDXKMA1?qs=0DP5yvOrqYnw8vb7hs35rQ%3D%3D) | 2025-04-22 | Aidan | power control
35409347 | mouser shipping | N/A | 7 | 0 |  | 1 | 7.99 | 7.99 | Link | mouser | 2025-04-07
91910467 | digikey Shipping | N/A | 7 | 0 |  | 1 | 6.99 | 6.99 | Link | digikey | 2025-04-07
CRCW080510K0FKEA | 10k resistor | Recovered | 7 | 1 | 20 left | 20 | .038 for 10 | 0.76 | Link | mouser (https://www.mouser.com/ProductDetail/Vishay-Dale/CRCW080510K0FKEA?qs=LOX6nxTstiZjDFtI%2F0c8Lw%3D%3D) | 2025-04-07 | Mackenzie
SFH11-PBPC-D10-ST-BK | 20 pin connector | Recovered | 7 | 1 | 2 left | 2 | 1.03 | 2.06 | Link | digikey (https://www.digikey.com/en/products/detail/SFH11-PBPC-D10-ST-BK/S9197-ND/1990090?curr=usd) | 2025-04-07 | Drew
LM358AN/NOPB | op amp | Recovered | 7 | 2 | 10 left | 10 | .504 for 10 | 5.04 | Link | mouser (https://www.mouser.com/ProductDetail/Texas-Instruments/LM358AN-NOPB?qs=QbsRYf82W3GCff2Ox79KQw%3D%3D) | 2025-04-07 | Mackenzie
SI8635BC-B-IS1 | digital to analog | Recovered | 7 | 3 | 2 left | 2 | 4.20 | 8.40 | Link | mouser (https://www.mouser.com/ProductDetail/Skyworks-Solutions-Inc/SI8635BC-B-IS1?qs=j6MGy4L9yX3ye6AkLBdJ3g%3D%3D) | 2025-04-07 | Mackenzie
HCNR201-500E | Photovoltaic Isolator | Recovered | 7 | 4 | 3 left | 3 | 4.97 | 14.91 | Link | mouser (https://www.mouser.com/ProductDetail/Broadcom-Avago/HCNR201-500E?qs=xnajaXqBF98KQiK5CjlDZw%3D%3D) | 2025-04-07 | Mackenzie
662108145021 | 8 pin connector | Recovered | 7 | 5 | 3 left | 3 | 2.38 | 7.14 | Link | mouser (https://www.mouser.com/ProductDetail/Wurth-Elektronik/662108145021?qs=E2PpAYvlWVu7csXQjAv5yw%3D%3D) | 2025-04-07 | Mackenzie
66201221022 | 12 pin connector | Recovered | 7 | 6 | 3 left | 3 | 0.81 | 2.43 | Link | mouser (https://www.mouser.com/ProductDetail/Wurth-Elektronik/66201221022?qs=E2PpAYvlWVvQA7Cy9fCxQA%3D%3D) | 2025-04-07 | Mackenzie
KSP2907ACTA | transistor - pnp | Recovered | 7 | 7 | 10 left | 10 | .189 for 10 | 1.89 | Link | mouser (https://www.mouser.com/ProductDetail/onsemi-Fairchild/KSP2907ACTA?qs=UMEuL5FsraBW3WF3NhwKWA%3D%3D) | 2025-04-07 | Mackenzie
CRCW080580K6FKEA | 80.6k resistor | Recovered | 7 | 8 | 20 left | 20 | .023 for 10 | 0.46 | Link | mouser (https://www.mouser.com/ProductDetail/Vishay-Dale/CRCW080580K6FKEA?qs=3kMMNJ4TLu2VW%252BzPqn0AiA%3D%3D) | 2025-04-07 | Mackenzie
RC0805FR-071KL | 1k resistor | Recovered | 7 | 9 | 10 left | 10 | .011 for 10 | 0.11 | Link | mouser (https://www.mouser.com/ProductDetail/YAGEO/RC0805FR-071KL?qs=1ogmaHw32WJjeGY0DHXakQ%3D%3D) | 2025-04-07 | Mackenzie
C0805C101K5GACTU | 100pF cap | Recovered | 7 | 10 | 20 left | 20 | .033 for 10 | 0.66 | Link | mouser (https://www.mouser.com/ProductDetail/KEMET/C0805C101K5GACTU?qs=XkGcM6gst%2F%252BrnN%2F4ZjqOvQ%3D%3D) | 2025-04-07 | Mackenzie
08051C104K4T2A | 0.1uF cap | Recovered | 7 | 11 | 24 left | 30 | .123 for 10 | 3.69 | Link | mouser (https://www.mouser.com/ProductDetail/KYOCERA-AVX/08051C104K4T2A?qs=46Fswce4YXm7yQcAJaRRKg%3D%3D) | 2025-04-07 | Mackenzie
293D106X9010B2TE3 | 10uF cap | Recovered | 7 | 12 | 20 left | 20 | .358 for 10 | 7.16 | Link | mouser (https://www.mouser.com/ProductDetail/Vishay-Sprague/293D106X9010B2TE3?qs=dw9IUK5PqlBRDYOm3aGkDw%3D%3D) | 2025-04-07 | Mackenzie
CRCW080549R9FKEA | 49.9 resistor | Recovered | 7 | 13 | 20 left | 20 | .026 for 10 | 0.52 | Link | mouser (https://www.mouser.com/ProductDetail/Vishay-Dale/CRCW080549R9FKEA?qs=kkyyugUlSrO9cI3mexpXiA%3D%3D) | 2025-04-07 | Mackenzie
CRCW1206300RFKEA | 300 resistor | Recovered | 7 | 14 | 10 left | 10 | .034 for 10 | 0.34 | Link | mouser (https://www.mouser.com/ProductDetail/Vishay-Dale/CRCW1206300RFKEA?qs=%252BMk1bzH0xpsQMmi1LBpmyg%3D%3D) | 2025-04-07 | Mackenzie
1N4148W-7-F | diodes | N/A | 7 | 15 | combined with 2.25, 0 left | 20 | .044 for 10 | 0.88 | Link | mouser (https://www.mouser.com/ProductDetail/Diodes-Incorporated/1N4148W-7-F?qs=LHX0FizJzg7Ae9ZM8LTAWw%3D%3D) | 2025-04-07 | Mackenzie, Aidan | optoelectronics, dc link
GUO40-12NO1 | rectifier | N/A | 7 | 16 | combined with 2.40, 0 left | 1 | 18.71 | 18.71 | Link | mouser (https://www.mouser.com/ProductDetail/IXYS/GUO40-12NO1?qs=jFjNEgmwGdfw6Jms4NyF%2Fw%3D%3D) | 2025-04-07 | Aidan | rectifier
2N7002-TP | mosfet | N/A | 7 | 17 | combined with 4.22, 0 left | 10 | .094 for 10 | 0.94 | Link | mouser (https://www.mouser.com/ProductDetail/833-2N7002-TP) | 2025-04-07 | Aidan | relay
83729083 | mouser shipping | N/A | 6 | 0 |  | 1 | 7.99 | 7.99 | Link | mouser | 2025-03-21
1N4148W-7-F | diodes | N/A | 6 | 1 | combined with 2.25, 0 left | 10 | .044 for 10 | 0.44 | Link | mouser (https://www.mouser.com/ProductDetail/Diodes-Incorporated/1N4148W-7-F?qs=LHX0FizJzg7Ae9ZM8LTAWw%3D%3D) | 2025-03-21 | Mackenzie, Aidan | optoelectronics, dc link
LT6654BHS6-1.25TRMPBF | iso15/dc, converter | N/A | 6 | 2 | combined with 2.58, 0 left | 1 | 5.56 | 5.56 | Link | mouser (https://www.mouser.com/ProductDetail/Analog-Devices/LT6654BHS6-1.25TRMPBF?qs=hVkxg5c3xu8qQEMa%252BoZSag%3D%3D) | 2025-03-21 | Aidan | power control
CGA5L1X7R1E106K160AD | 10 µF capacitor | N/A | 6 | 3 | combined with 2.46, 0 left | 3 | 1.07 | 3.21 | Link | mouser (https://www.mouser.com/ProductDetail/TDK/CGA5L1X7R1E106K160AD?qs=vG%252BtRDh6KwBb4XVCyciR9w%3D%3D) | 2025-03-21 | Aidan | power control
C0805C101K5GACTU | 100pF cap | Part of assembly | 6 | 4 | 0 left | 20 | .033 for 10 | 0.66 | Link | mouser (https://www.mouser.com/ProductDetail/KEMET/C0805C101K5GACTU?qs=XkGcM6gst%2F%252BrnN%2F4ZjqOvQ%3D%3D) | 2025-03-21 | Mackenzie
08051C104K4T2A | 0.1uF cap | Part of assembly | 6 | 5 | 0 left | 30 | .123 for 10 | 3.69 | Link | mouser (https://www.mouser.com/ProductDetail/KYOCERA-AVX/08051C104K4T2A?qs=46Fswce4YXm7yQcAJaRRKg%3D%3D) | 2025-03-21 | Mackenzie
293D106X9010B2TE3 | 10uF cap | Recovered | 6 | 6 | 4 left | 20 | .201 for 10 | 4.02 | Link | mouser (https://www.mouser.com/ProductDetail/Vishay-Sprague/293D106X9010B2TE3?qs=dw9IUK5PqlBRDYOm3aGkDw%3D%3D) | 2025-03-21 | Mackenzie
KSP2907ACTA | transistor - pnp | Recovered | 6 | 7 | 4 left | 10 | .146 for 10 | 1.46 | Link | mouser (https://www.mouser.com/ProductDetail/onsemi-Fairchild/KSP2907ACTA?qs=UMEuL5FsraBW3WF3NhwKWA%3D%3D) | 2025-03-21 | Mackenzie
CRCW080580K6FKEA | 80.6k resistor | Recovered | 6 | 8 | 8 left | 20 | .023 for 10 | 0.46 | Link | mouser (https://www.mouser.com/ProductDetail/Vishay-Dale/CRCW080580K6FKEA?qs=3kMMNJ4TLu2VW%252BzPqn0AiA%3D%3D) | 2025-03-21 | Mackenzie
RC0805FR-071KL | 1k resistor | Recovered | 6 | 9 | 10 left | 10 | .011 for 10 | 0.11 | Link | mouser (https://www.mouser.com/ProductDetail/YAGEO/RC0805FR-071KL?qs=1ogmaHw32WJjeGY0DHXakQ%3D%3D) | 2025-03-21 | Mackenzie
CRCW080510K0FKEA | 10k resistor | Recovered | 6 | 10 | 10 left | 20 | .038 for 10 | 0.76 | Link | mouser (https://www.mouser.com/ProductDetail/Vishay-Dale/CRCW080510K0FKEA?qs=LOX6nxTstiZjDFtI%2F0c8Lw%3D%3D) | 2025-03-21 | Mackenzie
CRCW080549R9FKEA | 49.9 resistor | Recovered | 6 | 11 | 20 left | 20 | .026 for 10 | 0.52 | Link | mouser (https://www.mouser.com/ProductDetail/Vishay-Dale/CRCW080549R9FKEA?qs=kkyyugUlSrO9cI3mexpXiA%3D%3D) | 2025-03-21 | Mackenzie
CRCW1206300RFKEA | 300 resistor | Recovered | 6 | 12 | 10 left | 10 | .034 for 10 | 0.34 | Link | mouser (https://www.mouser.com/ProductDetail/Vishay-Dale/CRCW1206300RFKEA?qs=%252BMk1bzH0xpsQMmi1LBpmyg%3D%3D) | 2025-03-21 | Mackenzie
LM358AN/NOPB | op amp | Recovered | 6 | 13 | 1 left | 10 | .507 for 10 | 5.07 | Link | mouser (https://www.mouser.com/ProductDetail/Texas-Instruments/LM358AN-NOPB?qs=QbsRYf82W3GCff2Ox79KQw%3D%3D) | 2025-03-21 | Mackenzie
SI8635BC-B-IS1 | digital to analog | Part of assembly | 6 | 14 | 0 left | 1 | 4.200 | 4.20 | Link | mouser (https://www.mouser.com/ProductDetail/Skyworks-Solutions-Inc/SI8635BC-B-IS1?qs=j6MGy4L9yX3ye6AkLBdJ3g%3D%3D) | 2025-03-21 | Mackenzie
HCNR201-500E | Photovoltaic Isolator | Part of assembly | 6 | 15 | 0 left | 2 | 4.97 | 9.94 | Link | mouser (https://www.mouser.com/ProductDetail/Broadcom-Avago/HCNR201-500E?qs=xnajaXqBF98KQiK5CjlDZw%3D%3D) | 2025-03-21 | Mackenzie | optoelectronics
NR6028T680M | SMD power inductor | Part of assembly | 6 | 16 | 0 left | 5 | 0.228 | 1.14 | Link | mouser (https://www.mouser.com/ProductDetail/TAIYO-YUDEN/NR6028T680M?qs=PzICbMaShUe1Bn1q%252BjvqyA%3D%3D) | 2025-03-21 | Drew | MCU
RR0816Q-750-D | 75ohm Resistor | Part of assembly | 6 | 17 | 0 left | 10 | .034 for 10 | 0.34 | Link | mouser (https://www.mouser.com/ProductDetail/Susumu/RR0816Q-750-D?qs=nCAm%252BcMdy9xZyrrAEWRV2A%3D%3D) | 2025-03-21 | Drew | MCU
SZ1SMB36CAT3G | TVS diode | Part of assembly | 6 | 18 | 0 left | 3 | 0.462 | 1.39 | Link | mouser (https://www.mouser.com/ProductDetail/Littelfuse/SZ1SMB36CAT3G?qs=sK5eIuwOod5ZlkyNXP0J4A%3D%3D&gad_source=1) | 2025-03-21 | Drew | MCU
dsPIC33CK256MP508T-I/PT | MCU chip | Part of assembly | 6 | 19 | 0 left | 1 | 3.62 | 3.62 | Link | mouser (https://www.mouser.com/ProductDetail/Microchip-Technology/dsPIC33CK256MP508T-I-PT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) | 2025-03-21 | Drew | MCU
LM2595S-3.3/NOPB | buck converter | Part of assembly | 6 | 20 | 0 left | 1 | 4.68 | 4.68 | Link | mouser (https://www.mouser.com/ProductDetail/Texas-Instruments/LM2595S-3.3-NOPB?qs=X1J7HmVL2ZF2pQj0svaMhw%3D%3D) | 2025-03-21 | Drew | MCU
KC2520Z8.00000C1KX00 | oscillator | Recovered | 6 | 21 | 1 left | 1 | 1.01 | 1.01 | Link | mouser (https://www.mouser.com/ProductDetail/KYOCERA-AVX/KC2520Z8.00000C1KX00?qs=rrS6PyfT74cbg89ZqaPNCA%3D%3D) | 2025-03-21 | Drew | MCU
08055C104KAZ2A | capacitor 0.1uF | Part of assembly | 6 | 22 | 0 left | 10 | 0.125 | 1.25 | Link | mouser (https://www.mouser.com/ProductDetail/KYOCERA-AVX/08055C104KAZ2A?qs=qS4bad6%2Fhx%2FmMvJL3brjow%3D%3D) | 2025-03-21 | Drew | MCU
ERJ-U03F1002V | 10k resistor | Recovered | 6 | 23 | 7 left | 10 | 0.042 | 0.42 | Link | mouser (https://www.mouser.com/ProductDetail/Panasonic/ERJ-3EKF1002V?qs=H7k1u0Mp9JSrGPQ5%2F5COuw%3D%3D) | 2025-03-21 | Drew | MCU
35018117 | mouser shipping | N/A | 5 | 0 |  | 1 | 7.99 | 7.99 | Link | mouser | 2025-02-25
LT6654BHS6-1.25TRMPBF | iso15/dc, converter | N/A | 5 | 1 | combined with 2.58, 0 left | 1 | 5.57 | 5.57 | Link | mouser (https://www.mouser.com/ProductDetail/Analog-Devices/LT6654BHS6-1.25TRMPBF?qs=hVkxg5c3xu8qQEMa%252BoZSag%3D%3D) | 2025-02-25 | Aidan | power control
GUO40-12NO1 | rectifier | N/A | 5 | 2 | combined with 2.40, 0 left | 1 | 13.73 | 13.73 | Link | mouser (https://www.mouser.com/ProductDetail/IXYS/GUO40-12NO1?qs=jFjNEgmwGdfw6Jms4NyF%2Fw%3D%3D) | 2025-02-25 | Aidan | rectifier
dsPIC33CK256MP508T-I/PT | MCU | Part of assembly | 5 | 3 | 0 left | 1 | 3.98 | 3.98 | Link | mouser (https://www.mouser.com/ProductDetail/Microchip-Technology/dsPIC33CK256MP508T-I-PT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) | 2025-02-25 | Drew | MCU
34891577 | mouser shipping | N/A | 4 | 0 |  | 1 | 8.89 | 8.89 | Link | mouser | 2025-02-12
08055C104KAZ2A | capacitor 0.1uF | Part of assembly | 4 | 1 | 0 left | 10 | 0.115 | 1.15 | Link | mouser (https://www.mouser.com/ProductDetail/KYOCERA-AVX/08055C104KAZ2A?qs=qS4bad6%2Fhx%2FmMvJL3brjow%3D%3D) | 2025-02-12 | Drew | MCU
SZ1SMB36CAT3G | TVS diode | Part of assembly | 4 | 2 | 0 left | 3 | 0.463 | 1.39 | Link | mouser (https://www.mouser.com/ProductDetail/Littelfuse/SZ1SMB36CAT3G?qs=sK5eIuwOod5ZlkyNXP0J4A%3D%3D&gad_source=1) | 2025-02-12 | Drew | MCU
SI8635BC-B-IS1 | digital to analog | Part of assembly | 4 | 3 | 0 left | 5 | 3.39 | 16.95 | Link | mouser (https://www.mouser.com/ProductDetail/Skyworks-Solutions-Inc/SI8635BC-B-IS1?qs=j6MGy4L9yX3ye6AkLBdJ3g%3D%3D) | 2025-02-12 | Mackenzie | optoelectronics
08051C104K4T2A | 0.1uF cap | Part of assembly | 4 | 4 | 0 left | 30 | .113 for 10 | 3.39 | Link | mouser (https://www.mouser.com/ProductDetail/KYOCERA-AVX/08051C104K4T2A?qs=46Fswce4YXm7yQcAJaRRKg%3D%3D) | 2025-02-12 | Mackenzie | optoelectronics
HCNR201-500E | Photovoltaic Isolator | Part of assembly | 4 | 5 | 0 left | 4 | 4.66 | 18.64 | Link | mouser (https://www.mouser.com/ProductDetail/Broadcom-Avago/HCNR201-500E?qs=xnajaXqBF98KQiK5CjlDZw%3D%3D) | 2025-02-12 | Mackenzie | optoelectronics
293D106X9010B2TE3 | 10uF cap | Part of assembly | 4 | 6 | 0 left | 20 | .196 for 10 | 3.92 | Link | mouser (https://www.mouser.com/ProductDetail/Vishay-Sprague/293D106X9010B2TE3?qs=dw9IUK5PqlBRDYOm3aGkDw%3D%3D) | 2025-02-12 | Mackenzie | optoelectronics
662108145021 | 8 pin connector | Part of assembly | 4 | 7 | keep with Mackenzie, 1 Aidan, 0 left | 3 | 2.38 | 7.14 | Link | mouser (https://www.mouser.com/ProductDetail/Wurth-Elektronik/662108145021?qs=E2PpAYvlWVu7csXQjAv5yw%3D%3D) | 2025-02-12 | Mackenzie, Aidan | optoelectronics
66201221022 | 12 pin connector | Part of assembly | 4 | 8 | keep with Mackenzie, 1 Aidan, 0 left | 4 | 0.81 | 3.24 | Link | mouser (https://www.mouser.com/ProductDetail/Wurth-Elektronik/66201221022?qs=E2PpAYvlWVvQA7Cy9fCxQA%3D%3D) | 2025-02-12 | Mackenzie, Aidan | optoelectronics
662104145021 | 4 pin connector | Part of assembly | 4 | 9 | keep with Mackenzie, 1 Aidan, 0 left | 2 | 2.07 | 4.14 | Link | mouser (https://www.mouser.com/ProductDetail/Wurth-Elektronik/662104145021?qs=E2PpAYvlWVuBlQTY%2FLbIwA%3D%3D) | 2025-02-12 | Mackenzie, Aidan | optoelectronics
CRCW080580K6FKEA | 80.6k resistor | Part of assembly | 4 | 10 | 0 left | 20 | .023 for 10 | 0.46 | Link | mouser (https://www.mouser.com/ProductDetail/Vishay-Dale/CRCW080580K6FKEA?qs=3kMMNJ4TLu2VW%252BzPqn0AiA%3D%3D) | 2025-02-12 | Mackenzie | optoelectronics
RC0805FR-071KL | 1k resistor | Recovered | 4 | 11 | 10 left | 20 | .011 for 10 | 0.22 | Link | mouser (https://www.mouser.com/ProductDetail/YAGEO/RC0805FR-071KL?qs=1ogmaHw32WJjeGY0DHXakQ%3D%3D) | 2025-02-12 | Mackenzie | optoelectronics
CRCW080510K0FKEA | 10k resistor | Part of assembly | 4 | 12 | 0 left | 20 | .023 for 10 | 0.46 | Link | mouser (https://www.mouser.com/ProductDetail/Vishay-Dale/CRCW080510K0FKEA?qs=LOX6nxTstiZjDFtI%2F0c8Lw%3D%3D) | 2025-02-12 | Mackenzie | optoelectronics
CRCW080549R9FKEA | 49.9 resistor | Part of assembly | 4 | 13 | 0 left | 20 | .023 for 10 | 0.46 | Link | mouser (https://www.mouser.com/ProductDetail/Vishay-Dale/CRCW080549R9FKEA?qs=kkyyugUlSrO9cI3mexpXiA%3D%3D) | 2025-02-12 | Mackenzie | optoelectronics
CRCW1206300RFKEA | 300 resistor | Part of assembly | 4 | 14 | 0 left | 10 | .027 for 10 | 0.27 | Link | mouser (https://www.mouser.com/ProductDetail/Vishay-Dale/CRCW1206300RFKEA?qs=%252BMk1bzH0xpsQMmi1LBpmyg%3D%3D) | 2025-02-12 | Mackenzie | optoelectronics
LM358AN/NOPB | op amp | Part of assembly | 4 | 15 | 0 left | 10 | .44 for 10 | 4.40 | Link | mouser (https://www.mouser.com/ProductDetail/Texas-Instruments/LM358AN-NOPB?qs=QbsRYf82W3GCff2Ox79KQw%3D%3D) | 2025-02-12 | Mackenzie | optoelectronics
A05KR05KR26E51A | 5 pin connector | Part of assembly | 4 | 16 | 0 left | 1 | 0.919 | 0.92 | Link | mouser (https://www.mouser.com/ProductDetail/JST-Commercial/A05KR05KR26E51A?qs=QpmGXVUTftGV4FfTih4Xjw%3D%3D) | 2025-02-12 | Drew | MCU
IKCM30F60GDXKMA1 | power control | N/A | 4 | 17 | combined with 1.3, 0 left | 1 | 17.04 | 17.04 | Link | mouser (https://www.mouser.com/ProductDetail/Infineon-Technologies/IKCM30F60GDXKMA1?qs=0DP5yvOrqYnw8vb7hs35rQ%3D%3D) | 2025-02-12 | Aidan | power control
RK73B2ATTD220J | 22 Ω resistor | N/A | 4 | 18 | combined with 2.47, 0 left | 10 | .014 for 10 | 0.14 | Link | mouser (https://www.mouser.com/ProductDetail/KOA-Speer/RK73B2ATTD220J?qs=qS2WN82jBqXgmHBWbpKu%2Fg%3D%3D) | 2025-02-12 | Aidan | power control
TLV1702AIDGKR | op amp 2 | N/A | 4 | 19 | combined with 2.50, 0 left | 1 | 1.58 | 1.58 | Link | mouser (https://www.mouser.com/ProductDetail/Texas-Instruments/TLV1702AIDGKR?qs=wrT8kFYR77%252BQt9zg9S%252BrrQ%3D%3D) | 2025-02-12 | Aidan | power control
NKE0305SC | 3.3/iso5, converter | N/A | 4 | 20 | combined with 2.60, 0 left | 1 | 8.28 | 8.28 | Link | mouser (https://www.mouser.com/ProductDetail/Murata-Power-Solutions/NKE0305SC?qs=T6KdyAiWzn9MdRiL8nlieA%3D%3D) | 2025-02-12 | Aidan | power control
CL31B104KBCNNNL | 0.1 µF capacitor | N/A | 4 | 21 | combined with 2.45, 0 left | 10 | .068 for 10 | 0.68 | Link | mouser (https://www.mouser.com/ProductDetail/Samsung-Electro-Mechanics/CL31B104KBCNNNL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) | 2025-02-12 | Aidan | dc link, power control
2N7002-TP | mosfet | Recovered | 4 | 22 | combined with 7.17, 6 left, 1 pcbv1, 6 trash | 3 | 0.13 | 0.39 | Link | mouser (https://www.mouser.com/ProductDetail/833-2N7002-TP) | 2025-02-12 | Aidan | relay
T495X476M035ATE200 | 47 µF capacitor | N/A | 4 | 23 | combined with 2.62, 0 left | 10 | 1.66 for 10 | 16.60 | Link | mouser (https://www.mouser.com/ProductDetail/KEMET/T495X476M035ATE200?qs=cr8T4Ugre44bJ%252BfXMSVKjA%3D%3D) | 2025-02-12 | Drew, Aidan | power control
352315319 | digikey Shipping | N/A | 3 | 0 |  | 1 | 6.99 | 6.99 | Link | digikey | 2024-11-18
B5B-PH-K-S | 5 pin connector | Recovered | 3 | 1 | 13 left, for programming | 10 | 0.203 | 2.03 | Link | digikey (https://www.digikey.com/en/products/detail/jst-sales-america-inc/B5B-PH-K-S/926614) | 2024-11-18 | Drew
ESR03EZPJ103 | 10k resistor (MCLR) | Part of assembly | 3 | 2 | 0 left | 10 | 0.068 | 0.68 | Link | digikey (https://www.digikey.com/en/products/detail/rohm-semiconductor/ESR03EZPJ103/1762722) | 2024-11-18 | Drew
108379499 | digikey Shipping | N/A | 2 | 0 |  | 1 | 6.99 | 6.99 | Link | digikey | 2024-11-13
34090832 | Mouser Shipping | N/A | 2 | 0 |  | 1 | 9.79 | 9.79 | Link | mouser | 2024-11-13
SFH11-PBPC-D10-ST-BK | 20 pin connector | Part of assembly | 2 | 1 | 0 left | 5 | 1.37 | 6.85 | Link | digikey (https://www.digikey.com/en/products/detail/SFH11-PBPC-D10-ST-BK/S9197-ND/1990090?curr=usd) | 2024-11-18 | Drew
TB006-508-03BE | 3 pin connector | Recovered | 2 | 1 | keep with Aidan, combined with 2.38, 6 left, 4 pcbv0, 1 pcbv1, 2 Drew | 10 | .389 for 10 | 3.89 | Link | mouser (https://www.mouser.com/ProductDetail/Same-Sky/TB006-508-03BE?qs=vLWxofP3U2zmvvLYJBQLMA%3D%3D) | 2024-11-13 | Drew, Aidan | microcontroller, power control
PREC003SAAN-RC | 3 pin connector for cable | Recovered | 2 | 2 | 1 left | 5 | 0.42 | 2.10 | Link | digikey (https://www.digikey.com/en/products/detail/PREC003SAAN-RC/S1012EC-03-ND/2774851?curr=usd) | 2024-11-18 | Drew
dsPIC33CK256MP508T-I/PT | MCU chip | Part of assembly | 2 | 2 | 0 left | 4 | 4.27 | 17.08 | Link | mouser (https://www.mouser.com/ProductDetail/Microchip-Technology/dsPIC33CK256MP508T-I-PT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) | 2024-11-13 | Drew
LM2595S-3.3/NOPB | buck converter | Part of assembly | 2 | 3 | 0 left | 3 | 5.14 | 15.42 | Link | digikey (https://www.digikey.com/en/products/detail/LM2595S-3.3-NOPB/LM2595S-3.3-NOPB-ND/363698?curr=usd) | 2024-11-18 | Drew
GRM155R71C104KA88D | 0.1 uF Capacitor | Recovered | 2 | 3 | 12 left | 50 | .016 for 10 | 0.80 | Link | mouser (https://www.mouser.com/ProductDetail/Murata-Electronics/GRM155R71C104KA88D?qs=8YPuuxuUzMJKePo9sU3A2g%3D%3D) | 2024-11-13 | Drew
NRC06ZOTRF | chip resistor | Part of assembly | 2 | 4 | 0 left | 10 | 0.024 | 0.24 | Link | digikey (https://www.digikey.com/en/products/detail/nic-components-corp/NRC06ZOTRF/18724531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) | 2024-11-18 | Drew
P090S-14T20BR10K | potentiometer | Part of assembly | 2 | 4 | 0 left | 5 | 1.19 | 5.95 | Link | mouser (https://www.mouser.com/ProductDetail/BI-Technologies-TT-Electronics/P090S-14T20BR10K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) | 2024-11-13 | Drew
430182043816 . | switch button | Part of assembly | 2 | 5 | 0 left | 10 | .479 for 10 | 4.79 | Link | mouser (https://www.mouser.com/ProductDetail/Wurth-Elektronik/430182043816?qs=wr8lucFkNMVm%252BwK7rSM84A%3D%3D) | 2024-11-13 | Drew
LTST-C190KGKT | Green LED | Part of assembly | 2 | 6 | 0 left | 10 | .111 for 10 | 1.11 | Link | mouser (https://www.mouser.com/ProductDetail/Lite-On/LTST-C190KGKT?qs=205qCy6M2Q%252BAdcgwUZktqw%3D%3D) | 2024-11-13 | Drew
CL05B104KP5NNNC | 0.1 microF capacitor | Part of assembly | 2 | 7 | 0 left | 6 | 0.091 | 0.55 | Link | mouser (https://www.mouser.com/ProductDetail/Samsung-Electro-Mechanics/CL05B104KP5NNNC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) | 2024-11-13 | Drew
CL10A106MP8NNNC | 10 microF capacitor | Part of assembly | 2 | 8 | 0 left | 10 | .053 for 10 | 0.53 | Link | mouser (https://www.mouser.com/ProductDetail/Samsung-Electro-Mechanics/CL10A106MP8NNNC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) | 2024-11-13 | Drew
GRM31CC80E227ME11L | 220 uF capacitor | Recovered | 2 | 9 | 7 left | 10 | .488 for 10 | 4.88 | Link | mouser (https://www.mouser.com/ProductDetail/Murata-Electronics/GRM31CC80E227ME11L?qs=1iITwRmBZUb1xIxq8qqJhw%3D%3D) | 2024-11-13 | Drew
1N5822 | Diode Schottky | Recovered | 2 | 10 | 4 left | 10 | .206 for 10 | 2.06 | Link | mouser (https://www.mouser.com/ProductDetail/STMicroelectronics/1N5822?qs=JV7lzlMm3yJ50hlrGV6%252BnQ%3D%3D) | 2024-11-13 | Drew
MH1608-601Y | Ferrite Bead | Recovered | 2 | 11 | 9 left | 10 | .042 for 10 | 0.42 | Link | mouser (https://www.mouser.com/ProductDetail/Bourns/MH1608-601Y?qs=aqFbwuCjQoleaQpx2htlzw%3D%3D&gad_source=1) | 2024-11-13 | Drew
NR6028T680M | SMD power inductor | Part of assembly | 2 | 12 | 0 left | 5 | 0.291 | 1.45 | Link | mouser (https://www.mouser.com/ProductDetail/TAIYO-YUDEN/NR6028T680M?qs=PzICbMaShUe1Bn1q%252BjvqyA%3D%3D) | 2024-11-13 | Drew
RN73A1J470RFTD | 470ohm Resistor | Part of assembly | 2 | 13 | 0 left | 10 | .083 for 10 | 0.83 | Link | mouser (https://www.mouser.com/ProductDetail/TE-Connectivity-Holsworthy/RN73A1J470RFTD?qs=OZVHsXXMeBWMum6SvfGsUw%3D%3D) | 2024-11-13 | Drew
CRCW060310K0FKEC | 10kOhm resistor | Recovered | 2 | 14 | 9 left | 20 | .015 for 10 | 0.30 | Link | mouser (https://www.mouser.com/ProductDetail/Vishay-Dale/CRCW060310K0FKEC?qs=DhCTQV%252BB7kVUX5brQUG3LA%3D%3D) | 2024-11-13 | Drew
ERJ-3EKF1001V | 1kohm resistor | Recovered | 2 | 15 | 11 left | 20 | .015 for 10 | 0.30 | Link | mouser (https://www.mouser.com/ProductDetail/Panasonic/ERJ-3EKF1001V?qs=H7k1u0Mp9JTM8yQxOuvoDg%3D%3D) | 2024-11-13 | Drew
RR0816P-331-D | 330ohm resistor | Recovered | 2 | 16 | 4 left | 10 | .022 for 10 | 0.22 | Link | mouser (https://www.mouser.com/ProductDetail/Susumu/RR0816P-331-D?qs=nCAm%252BcMdy9xrDTw9NRpXlA%3D%3D) | 2024-11-13 | Drew
ERJ-3EKF1000V | 100 ohm resistor | Part of assembly | 2 | 17 | 0 left | 10 | .02 for 10 | 0.20 | Link | mouser (https://www.mouser.com/ProductDetail/Panasonic/ERJ-3EKF1000V?qs=H7k1u0Mp9JS7i8KGO5m47A%3D%3D) | 2024-11-13 | Drew
RR0816Q-750-D | 75ohm Resistor | Part of assembly | 2 | 18 | 0 left | 40 | .034 for 10 | 1.36 | Link | mouser (https://www.mouser.com/ProductDetail/Susumu/RR0816Q-750-D?qs=nCAm%252BcMdy9xZyrrAEWRV2A%3D%3D) | 2024-11-13 | Drew
IRM-15-15 | AC/DC Converter | Part of assembly | 2 | 19 | 0 left | 2 | 9.39 | 18.78 | Link | mouser (https://www.mouser.com/ProductDetail/MEAN-WELL/IRM-15-15?qs=WkdRfq4wf1N170hhVSUvEA%3D%3D) | 2024-11-13 | Drew
KC2520Z8.00000C1KX00 | oscillator | Part of assembly | 2 | 20 | 0 left | 5 | 1.07 | 5.35 | Link | mouser (https://www.mouser.com/ProductDetail/KYOCERA-AVX/KC2520Z8.00000C1KX00?qs=rrS6PyfT74cbg89ZqaPNCA%3D%3D) | 2024-11-13 | Drew
TTL-232R-RPI | USB cable | Recovered | 2 | 21 | 1 left | 1 | 20.29 | 20.29 | Link | mouser (https://www.mouser.com/ProductDetail/FTDI/TTL-232R-RPI?qs=3tuk1l7PSbNqj0mOeA5IPw%3D%3D) | 2024-11-13 | Drew
C0805C101K5GACTU | 100pF cap | Part of assembly | 2 | 22 | 0 left | 20 | .03 for 10 | 0.60 | Link | mouser (https://www.mouser.com/ProductDetail/KEMET/C0805C101K5GACTU?qs=XkGcM6gst%2F%252BrnN%2F4ZjqOvQ%3D%3D) | 2024-11-13 | Mackenzie
08051C104K4T2A | 0.1uF cap | Part of assembly | 2 | 23 | 0 left | 30 | .117 for 10 | 3.51 | Link | mouser (https://www.mouser.com/ProductDetail/KYOCERA-AVX/08051C104K4T2A?qs=46Fswce4YXm7yQcAJaRRKg%3D%3D) | 2024-11-13 | Mackenzie
293D106X9010B2TE3 | 10uF cap | Part of assembly | 2 | 24 | 0 left | 20 | 0.206 for 10 | 4.12 | Link | mouser (https://www.mouser.com/ProductDetail/Vishay-Sprague/293D106X9010B2TE3?qs=dw9IUK5PqlBRDYOm3aGkDw%3D%3D) | 2024-11-13 | Mackenzie
1N4148W-7-F | diodes | Recovered | 2 | 25 | keep with Aidan, combined with 6.1 & 7.15, 26 left | 20 | .051 for 10 | 1.02 | Link | mouser (https://www.mouser.com/ProductDetail/Diodes-Incorporated/1N4148W-7-F?qs=LHX0FizJzg7Ae9ZM8LTAWw%3D%3D) | 2024-11-13 | Mackenzie, Aidan | optoelectronics, dc link
662108145021 | 8 pin connector | Part of assembly | 2 | 26 | 0 left | 2 | 2.38 | 4.76 | Link | mouser (https://www.mouser.com/ProductDetail/Wurth-Elektronik/662108145021?qs=E2PpAYvlWVu7csXQjAv5yw%3D%3D) | 2024-11-13 | Mackenzie
66201221022 | 12 pin connector | Part of assembly | 2 | 27 | 0 left | 2 | 0.892 | 1.78 | Link | mouser (https://www.mouser.com/ProductDetail/Wurth-Elektronik/66201221022?qs=E2PpAYvlWVvQA7Cy9fCxQA%3D%3D) | 2024-11-13 | Mackenzie
662104145021 | 4 pin connector | Part of assembly | 2 | 28 | 0 left | 1 | 2.07 | 2.07 | Link | mouser (https://www.mouser.com/ProductDetail/Wurth-Elektronik/662104145021?qs=E2PpAYvlWVuBlQTY%2FLbIwA%3D%3D) | 2024-11-13 | Mackenzie
KSP2907ACTA | transistor - pnp | Part of assembly | 2 | 29 | 0 left | 10 | .133 for 10 | 1.33 | Link | mouser (https://www.mouser.com/ProductDetail/onsemi-Fairchild/KSP2907ACTA?qs=UMEuL5FsraBW3WF3NhwKWA%3D%3D) | 2024-11-13 | Mackenzie
CRCW080580K6FKEA | 80.6k resistor | Part of assembly | 2 | 30 | 0 left | 20 | .023 for 10 | 0.46 | Link | mouser (https://www.mouser.com/ProductDetail/Vishay-Dale/CRCW080580K6FKEA?qs=3kMMNJ4TLu2VW%252BzPqn0AiA%3D%3D) | 2024-11-13 | Mackenzie
RC0805FR-071KL | 1k resistor | Part of assembly | 2 | 31 | 0 left | 10 | .013 for 10 | 0.13 | Link | mouser (https://www.mouser.com/ProductDetail/YAGEO/RC0805FR-071KL?qs=1ogmaHw32WJjeGY0DHXakQ%3D%3D) | 2024-11-13 | Mackenzie
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

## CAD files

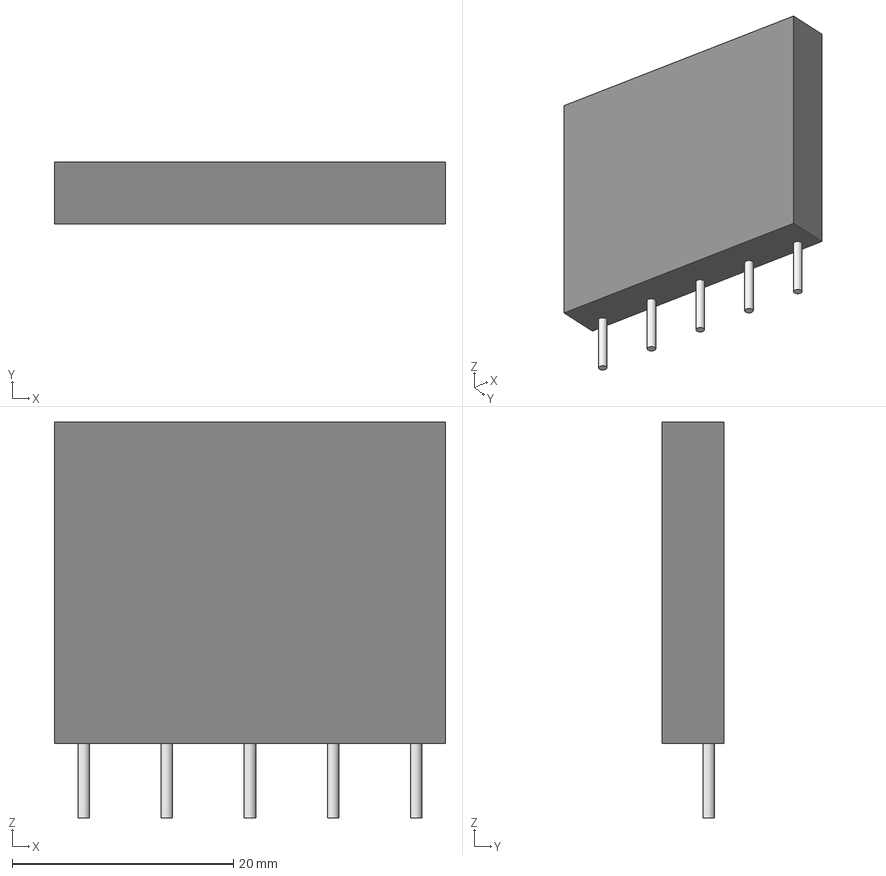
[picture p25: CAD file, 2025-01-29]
power_backup/SIP5-GUFP_LTF.step
35.3 x 5.59 x 35.7 mm

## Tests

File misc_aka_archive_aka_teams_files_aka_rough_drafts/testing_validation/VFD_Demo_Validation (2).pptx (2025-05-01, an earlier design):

## Input Voltage Level

FSR 1

## Power converters shall convert 15 VDC to isolated 15 VDC.

Vin (V) | Vin,pp (mV) | Vout (V) | Vout,pp (mV)
9.1 | 200 | 15.1 | 400
15.1 | 500 | 15.0 | 400
20.9 | 500 | 14.9 | 400
27.0 | 500 | 15.3 | 500
33.040 | 578 | 14.887 | 264
35.804 | 503 | 14.887 | 264

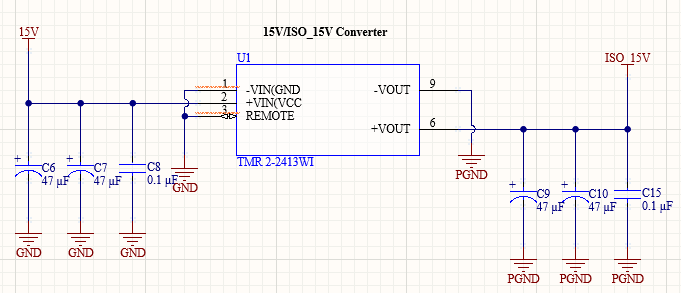
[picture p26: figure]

Iout (mA) | Vout (V)
12 | 14.959
25 | 14.951
50 | 14.937
75 | 14.924
100 | 14.912
125 | 14.898
134 | 14.893

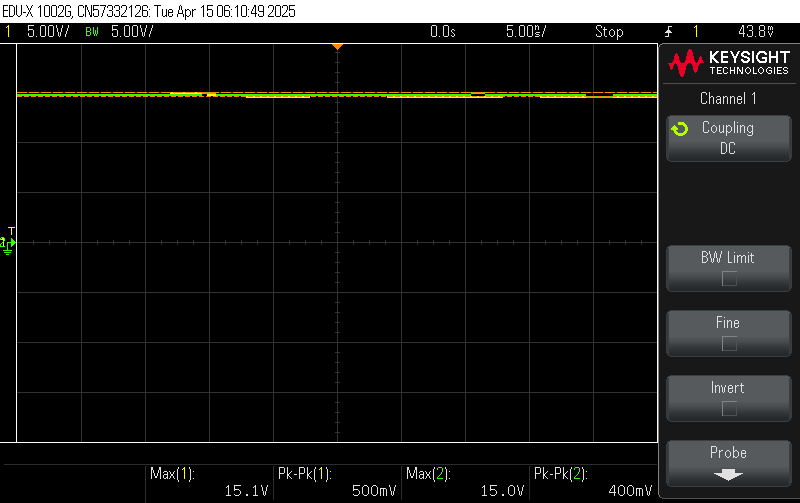
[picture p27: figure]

Vin = 9 V

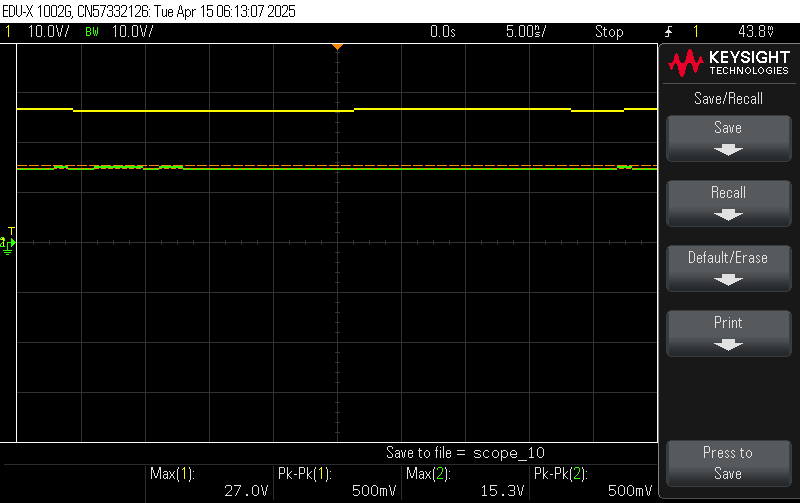
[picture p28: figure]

Vin = 15 V

Vin = 21 V

Vin = 27 V

## Power converters shall convert 15 VDC to 3.3 VDC.

Vin (V) | Vout (V)
16.0 | 3.003
15.5 | 3.2997
15.0 | 3.2997
14.5 | 3.2995

Load (mA) | Vout (V)
0 | 3.2993
30 | 3.2952
50 | 3.2824
72 | 3.2812
95 | 3.2601
122 | 3.2512
153 | 3.2243

## Power converters shall convert 3.3 VDC to isolated 5 VDC.

Vin (V) | Vin,pp (mV) | Vout (V) | Vout,pp (mV)
2.8 | 500 | 4.9 | 500
3.2 | 500 | 4.8 | 500
3.3 | 500 | 5.3 | 500
3.6 | 900 | 5.7 | 500

Iout (mA) | Vout (V)
12 | 5.381
50 | 5.188
100 | 4.981
150 | 4.782
200 | 4.581

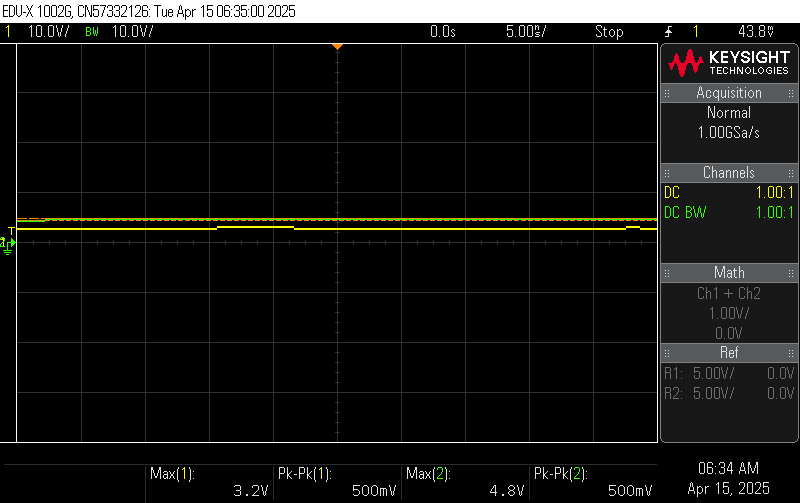
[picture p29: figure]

Vin = 2.8 V

Vin = 3.2 V

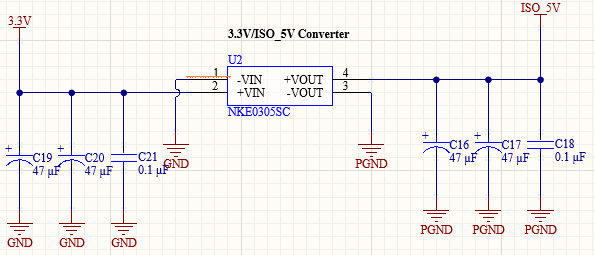
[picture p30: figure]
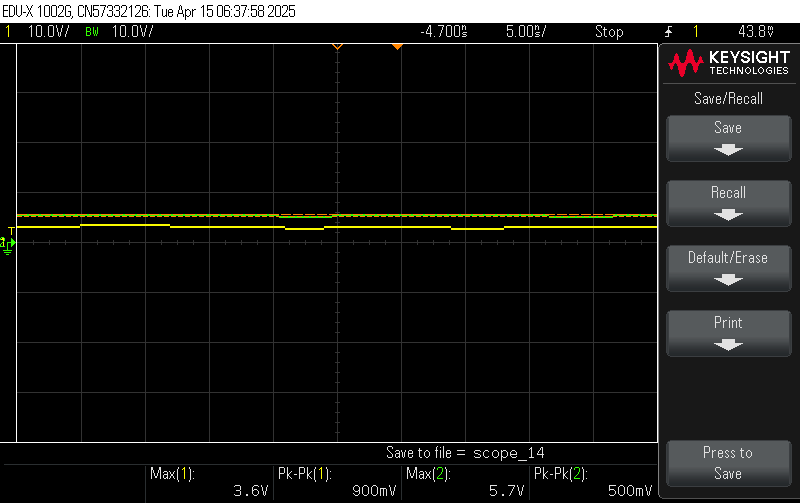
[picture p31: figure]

Vin = 3.3 V

Vin = 3.6 V

## System shall convert 15 VDC to isolated 15 VDC , 3.3 VDC, and isolated 5 VDC.

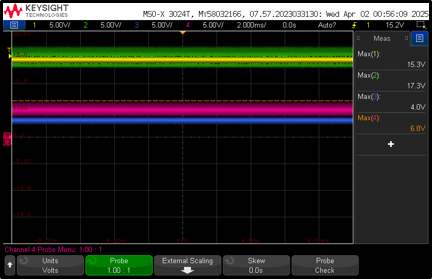
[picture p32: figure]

Converter | Vspec [V] | Vmin [V] | Vnom [V] | Vmax [V]
2-Phase to 15V | 15.0 | | 15.0
15V to Iso15V | 15.0 | 14.9 | 15.1 | 15.3
15V to 3.3V | 3.3 | 3.2 | 3.3 | 3.3
3.3V to Iso5V | 5.0 | 4.6 | 5.1 | 5.6

## Power converters shall convert 120 VAC to 15 VDC.

Vin (VAC) | Vout (VDC)
118 | 15.0

## On/Off Functionality

FSR 2

## Relay shall toggle the motor with the relay signal.

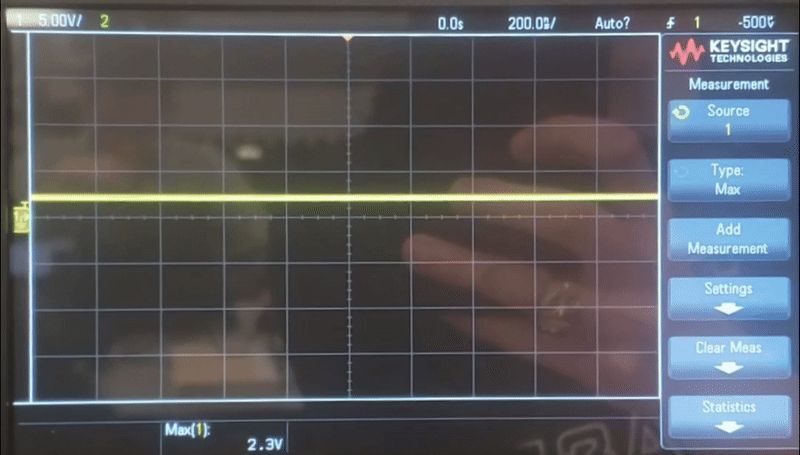
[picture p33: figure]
A screen shot of a graph

Vin
5-40V | Contact Voltage | Rated up to required voltage
15V | Coil Voltage
5V | Relay Signal

## Digital to power shall convert the relay signal from 3.3 VDC to 5 VDC.

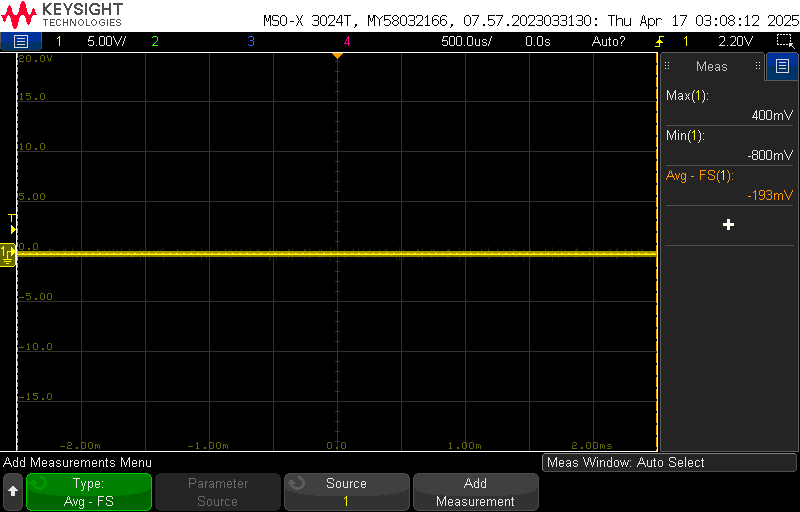
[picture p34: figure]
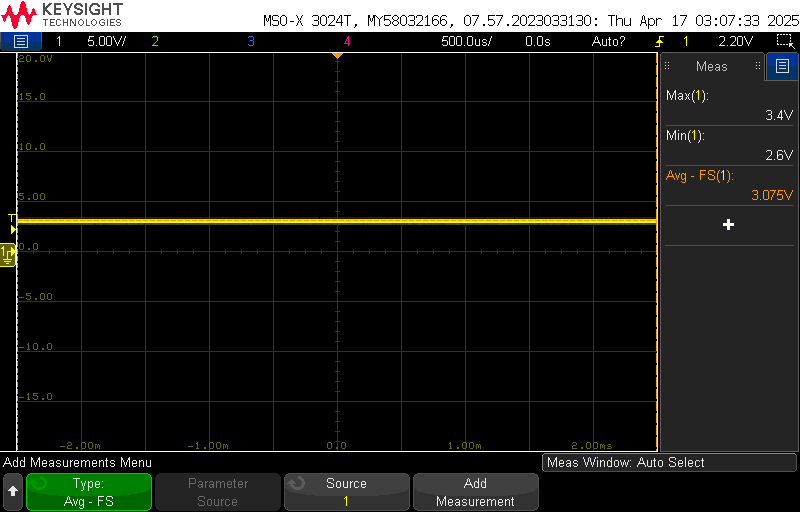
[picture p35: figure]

~0 V when button off 3.4 V before isolator 5.8V after isolator

## MCU shall toggle the relay signal to 3.3 VDC with the button signal.

Relay
On | Off
3.281V | -.045V

## Button shall toggle the button signal to 3.3 VDC with a button press.

Button
Not Pressed | Pressed
3.25V | -.048V

## System shall toggle the motor between on and off state with a button press.

On/Off Button

A person working on a circuit board

## Motor Runs at Correct Voltage

FSR 3

## Rectifier shall convert 120 VAC to 112 VDC.


## PWM Signals

FSR 4

## Power control shall invert three high and three low 5 VDC PWM signals into three modified sine waves.

Measured Line to Line Waveforms


Expected Line to Line Waveforms


## Digital to power shall convert three high and three low PWM signals from 3.3 VDC to 5 VDC.


U
V
W


3.4 V 6.0-6.2 V

## MCU shall generate three high and three low 3.3 VDC PWM signals with the knob signal.

U
V
W

## System shall change the motor speed with the knob signal.

Measured Line to Line Waveforms

Speed Knob

A person working on a circuit board

## Continued

Knob
Positions | Voltage
Low | -.045V
Middle | 1.603V
High | 3.285

PWM
Signal | Frequency (kHz) | Minimum Voltage | Maximum Voltage | Phase Offset (degrees) | Low Pot Value - Low Frequency | High Pot Value - High Frequency
1H | 1 | -0.13 | 3.65V | 0 | TRUE | TRUE
1L | 1 | -0.13 | 3.65V | 0 | TRUE | TRUE
2H | 1 | -0.13 | 3.65V | 120 | TRUE | TRUE
2L | 1 | -0.13 | 3.65V | 120 | TRUE | TRUE
3H | 1 | -0.13 | 3.65V | 240 | TRUE | TRUE
3L | 1 | -0.13 | 3.65V | 240 | TRUE | TRUE

## Motor On/Off LED

FSR 5

## MCU shall toggle the motor on/off LED signal to 3.3 VDC with the button signal.

~0 V when button off 3.4 V when button on

## System shall toggle the motor on/off LED between on and off states with the motor on/off signal.


Motor LED (blue) off when on/off button is off Motor LED (blue) on when on/off button is on
(motor is off) (motor is on)

## System On/Off LED

FSR 6

## MCU shall toggle the circuit on/off LED signal to 3.3 VDC when the board receives power.

3.4V when circuit is on

## System shall toggle the circuit on/off LED when the board is connected to power with the circuit on/off signal


System LED (red) off when 15 V not applied System LED (red) on when 15 V applied
(system is off) (system is on)

## Diagnostic Feedback

FSR 7

## Diagnostic feedback circuit shall transport the voltage, current, and temperature signals from across the isolation barrier to the MCU.

| Input Voltage | Output Voltage
bus.v | 15 V | 3.9 V
ilim.v | 15 V | 3.9 V
ips.temp | 15 V | 3.9 V

## Power Control shall generate 60 VDC voltage, current, and temperature feedback signals.

| | Output Voltage | Notes
bus.v | voltage
ilim.v | current | 0 | Built for 30 A, 2 A results in zero
ips.temp | temperature

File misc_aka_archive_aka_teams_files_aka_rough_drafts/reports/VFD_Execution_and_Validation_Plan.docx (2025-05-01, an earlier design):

VFD Motor Controller

Mackenzie Miller

Andrew Nguyen

Aidan Rader

Ryan Regan

Execution and Validation Plan

REVISION – 1

28 April 2025

Execution Plan


Figure 1: Execution Plan Fall 2024


Figure 2: Execution Plan Spring 2025

Validation Plan

Paragraph # | Test Name | Success Criteria | Methodology | Status | Responsible Engineer(s)
3.2.3.11 | 15 VDC to Isolated 15 VDC Conversion | Power converters shall convert 15 VDC to isolated 15 VDC. | Apply 15 VDC input using a DC power supply. Verify 15 VDC output using an oscilloscope. | Tested | Aidan
3.2.3.12 | 15 VDC to 3.3 VDC Conversion | Power converters shall convert 15 VDC to 3.3 VDC. | Apply 15 VDC input using a DC power supply. Verify 3.3 VDC output using an oscilloscope. | Tested | Drew
3.2.3.13 | 3.3 VDC to Isolated 5 VDC Conversion | Power converters shall convert 3.3 VDC to isolated 5 VDC. | Apply 3.3 VDC input using a DC power supply. Verify 5 VDC output using an oscilloscope. | Tested | Aidan
3.2.3.14 | Low Voltage Auxiliary Power | System shall convert 15 VDC to isolated 15 VDC , 3.3 VDC, and isolated 5 VDC. | Apply 15 VDC input using a DC power supply. Verify 15 VDC , 3.3 VDC, and 5 VDC outputs using an oscilloscope. | Tested | Mackenzie, Drew, Aidan
3.2.3.15 | 120 VAC to 15 VDC Conversion | Power converters shall convert 120 VAC to isolated 15 VDC. | Apply 120 VAC input using a 120 VAC outlet. Verify 15 VDC output using an oscilloscope. | Tested | Drew
3.2.3.16 | 120 VAC Auxiliary Power | System shall convert 120 VAC to 15 VDC, isolated 15 VDC , 3.3 VDC, and isolated 5 VDC. | Apply 120 VAC input using a 120 VAC outlet. Verify 15 VDC, 15 VDC , 3.3 VDC, and 5 VDC outputs using an oscilloscope. | Tested | Mackenzie, Drew, Aidan
3.2.3.17 | Relay | Relay shall toggle the motor with the relay signal. | Apply 15 VDC coil voltage, 10 VDC contact voltage, and 5 VDC relay signal using a DC power supply. Verify 10 VDC output using an oscilloscope. | Tested | Aidan
3.2.3.18 | Relay Signal Isolation | Digital to power shall convert the relay signal from 3.3 VDC to 5 VDC. | Apply 5 VDC supply voltage, 3.3 VDC supply voltage, and 3.3 VDC relay signal using a DC power supply. Verify 5 VDC output using an oscilloscope. | Tested | Mackenzie
3.2.3.19 | Relay Signal Generation | MCU shall toggle the relay signal to 3.3 VDC with the button signal. | Apply 3.3 VDC supply voltage and 3.3 VDC button signal using a DC power supply. Verify 3.3 VDC output using an oscilloscope. | Tested | Drew, Ryan
3.2.3.20 | Firmware Relay Signal Generation | Dev board shall toggle the relay signal to 3.3 VDC with the button signal. | (On the dev board) Apply 3.3 VDC supply voltage and 3.3 VDC button signal using a DC power supply. Verify 3.3 VDC output using an oscilloscope. | Tested | Ryan
3.2.3.21 | Button Signal Generation | Button shall toggle the button signal to 3.3 VDC with a button press. | Apply 3.3 VDC supply voltage using a DC power supply and initiate a button press. Verify 3.3 VDC output using an oscilloscope. | Tested | Drew
3.2.3.22 | On/Off Button | System shall toggle the motor between on and off state with a button press. | Apply 15 VDC coil voltage, 10 VDC contact voltage, 5 VDC supply voltage, and 3.3 VDC supply voltage using a DC power supply. Initiate one button press and later a second button press. Verify the motor rotates after the first button press and stops after the second button press using a video. | Tested | All
3.2.3.23 | 10 VAC to 12 VDC Rectification | Rectifier shall convert 120 VAC to 112 VDC. | Apply 120 VAC input using a 120 VAC outlet. Verify 112 VDC output using an oscilloscope. | Tested | Aidan
3.2.3.24 | 120 VAC to 112 VDC Rectification | Rectifier shall convert 120 VAC to 112 VDC. | Apply 120 VAC input using a 120 VAC outlet. Verify 112 VDC output using an oscilloscope. | Tested | Aidan
3.2.3.25 | Power Control | Power control shall invert three high and three low 5 VDC PWM signals into three modified sine waves. | Apply 40 VDC bus voltage and 15 VDC supply voltage using a DC power supply. Apply three high and three low 5 VDC PWM signals at 120˚ phase shifts using a function generator. Verify three modified sine waves at 120˚ phase shifts using an oscilloscope. | Tested | Aidan
3.2.3.26 | PWM Signal Isolation | Digital to power shall convert three high and three low PWM signals from 3.3 VDC to 5 VDC. | Apply isolated 5 VDC supply voltage and 3.3 VDC supply voltage using a DC power supply. Apply three high and three low 3.3 VDC PWM signals at 120˚ phase shifts using a function generator. Verify three high and three low 5 VDC PWM signals at 120˚ phase shifts using an oscilloscope. | Tested | Mackenzie
3.2.3.27 | PWM Signal Generation | MCU shall generate three high and three low 3.3 VDC PWM signals with the knob signal. | Apply 3.3 VDC supply voltage and 3.3 VDC speed knob signal using a DC power supply. Verify three high and three low 3.3 VDC PWM signals at 120˚ phase shifts using an oscilloscope. | Tested | Drew, Ryan
3.2.3.28 | Knob Signal Generation | Rotating potentiometer changes frequency to speed up and slow down motor. | Oscilloscope each signal output, spin knob and ensure the motor speed varies as expected. | Tested | Drew, Ryan
3.2.3.29 | Firmware PWM Signal Generation | Dev board shall generate three high and three low 3.3 VDC PWM signals with the knob signal. | (On dev board) Apply 3.3 VDC supply voltage and 3.3 VDC speed knob signal using a DC power supply. Verify three high and three low 3.3 VDC PWM signals at 120˚ phase shifts using an oscilloscope. | Tested | Ryan
3.2.3.30 | Firmware Knob Signal Generation | Rotating dev board potentiometer changes frequency to speed up and slow down motor. | (On dev board) Oscilloscope each signal output, spin knob and ensure the motor speed varies as expected. | Tested | Ryan
3.2.3.31 | Low Voltage PWM Control | System shall change the motor speed with the knob signal. | Apply 40 VDC bus voltage, 15 VDC supply voltage, isolated 5 VDC supply voltage and 3.3 VDC supply voltage using a DC power supply. Verify the motor rotates at a different speed after a knob turn using a video. | Tested | All
3.2.3.32 | 112 VDC PWM Control | System shall change the motor speed with the knob signal. | Apply 112 VDC bus voltage, 15 VDC supply voltage, isolated 5 VDC supply voltage and 3.3 VDC supply voltage using a DC power supply. Verify the motor rotates at a different speed after a knob turn using a video. | Untested | All
3.2.3.33 | Motor On/Off Signal Generation | MCU shall toggle the motor on/off LED signal to 3.3 VDC with the button signal. | Directly inject 15V to MCU and use multimeter at the motor LED via. | Tested | Drew, Ryan
3.2.3.34 | Motor On/Off LED | System shall toggle the motor on/off LED between on and off states with the motor on/off signal. | Directly inject 15V to MCU, then press relay toggle button and ensure the motor LED toggles. | Tested | Drew, Ryan
3.2.3.35 | System On/Off Signal Generation | MCU shall toggle the circuit on/off LED signal to 3.3 VDC when the board receives power. | Directly inject 15V to MCU and use multimeter at the system LED via. | Tested | Drew, Ryan
3.2.3.36 | System On/Off LED | System shall toggle the circuit on/off LED when the board is connected to power with the circuit on/off signal | Directly inject 15V to MCU and ensure the system LED turns on. | Tested | Drew, Ryan
3.2.3.37 | Firmware Motor On/Off LED Signal Generation | Firmware shall toggle the dev board's on/off LED signal to 3.3 VDC with the button signal. | Directly inject 15V to dev board and use multimeter at the motor LED via. | Tested | Ryan
3.2.3.38 | Firmware Motor On/Off LED | Firmware shall toggle the dev board's on/off LED between on and off states with the motor on/off signal. | Directly inject 15V to dev board, then press relay toggle button and ensure the motor LED toggles. | Tested | Ryan
3.2.3.39 | Firmware System LED Signal Generation | Firmware shall toggle the dev board's on/off LED signal to 3.3 VDC when the board receives power. | Directly inject 15V to dev board and use multimeter at the system LED via. | Tested | Ryan
3.2.3.40 | Firmware System LED | Firmware shall toggle the dev board's on/off LED when the board is connected to power with the circuit on/off signal | Directly inject 15V to dev board and ensure the system LED turns on. | Tested | Ryan
3.2.3.41 | Computer Display | MCU will display diagnostic feedback information to the UART console on a computer running MPLAB X IDE. | Connect system to MPLAB X IDE using a laptop and USB-UART cable. Verify diagnostic print statements are being output to UART console. | Untested | Drew, Ryan
3.2.3.42 | Diagnostic Feedback Signal Isolation | Diagnostic feedback circuit shall transport the voltage, current, and temperature signals from across the isolation barrier to the MCU. | Apply 15 VDC supply voltage, isolated 15 VDC supply voltage, and three 15 VDC feedback signals using a DC power supply. Verify three 15 VDC outputs using an oscilloscope. | Untested | Mackenzie
3.2.3.43 | Diagnostic Feedback Signal Generation | Power Control shall generate 60 VDC voltage, current, and temperature feedback signals. | Apply 40 VDC bus voltage and 15 VDC supply voltage using a DC power supply. Apply three high and three low 5 VDC PWM signals at 120˚ phase shifts using a function generator. Verify three 60 VDC outputs using an oscilloscope. | Untested | Aidan
3.2.3.44 | Diagnostic Feedback | System shall send the voltage, current, and temperature signals to the computer display. | Each feedback signal will be verified through the UART console output. | Untested | All

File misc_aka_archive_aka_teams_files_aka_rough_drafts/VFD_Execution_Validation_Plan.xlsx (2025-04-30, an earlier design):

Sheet: 404 Execution
Execution Plan 1/16/2025-4/28/2025
 | 2025-01-16 | 2025-01-23 | 2025-01-30 | 2025-02-06 | 2025-02-13 | 2025-02-20 | 2025-02-27 | 2025-03-06 | 2025-03-13 | 2025-03-20 | 2025-03-27 | 2025-04-03 | 2025-04-10 | 2025-04-17 | 2025-04-24 | Date
PCBv1s Design (Full Design Review) |  |  |  |  |  |  |  |  |  |  |  |  |  |  |  | 2025-01-28
Status Update Presentation 1 |  |  |  |  |  |  |  |  |  |  |  |  | Not Started |  |  | 2025-01-29
PCBv1s Order |  |  |  |  |  |  |  |  |  |  |  |  | In Progress |  |  | 2025-02-06
Parts Order 4 |  |  |  |  |  |  |  |  |  |  |  |  | Completed |  |  | 2025-02-11
Firmware Validation |  |  |  |  |  |  |  |  |  |  |  |  | Behind Schedule |  |  | 2025-02-12
Status Update Presentation 2 |  |  |  |  |  |  |  |  |  |  |  |  |  |  |  | 2025-02-12
Status Update Presentation 3 |  |  |  |  |  |  |  |  |  |  |  |  |  |  |  | 2025-02-26
PCBv1s Assembly |  |  |  |  |  |  |  |  |  |  |  |  |  |  |  | 2025-03-19
MCU/Firmware Integration |  |  |  |  |  |  |  |  |  |  |  |  |  |  |  | 2025-03-19
Status Update Presentation 4 |  |  |  |  |  |  |  |  |  |  |  |  |  |  |  | 2025-03-19
Auxilary Power Integration |  |  |  |  |  |  |  |  |  |  |  |  |  |  |  | 2025-04-02
Status Update Presentation 5 |  |  |  |  |  |  |  |  |  |  |  |  |  |  |  | 2025-04-02
PWM Control Integration |  |  |  |  |  |  |  |  |  |  |  |  |  |  |  | 2025-04-03
Relay Control Integration |  |  |  |  |  |  |  |  |  |  |  |  |  |  |  | 2025-04-07
System Integration |  |  |  |  |  |  |  |  |  |  |  |  |  |  |  | 2025-04-07
System Testing |  |  |  |  |  |  |  |  |  |  |  |  |  |  |  | 2025-04-16
Final Presentation |  |  |  |  |  |  |  |  |  |  |  |  |  |  |  | 2025-04-16
Diagnostic Feedback Integration |  |  |  |  |  |  |  |  |  |  |  |  |  |  |  | 2025-04-24
System Validation |  |  |  |  |  |  |  |  |  |  |  |  |  |  |  | 2025-04-24
Final Demonstration |  |  |  |  |  |  |  |  |  |  |  |  |  |  |  | 2025-04-24
Engineering Project Showcase |  |  |  |  |  |  |  |  |  |  |  |  |  |  |  | 2025-04-25
Final Report |  |  |  |  |  |  |  |  |  |  |  |  |  |  |  | 2025-04-28

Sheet: Validation_v0
Paragraph # | Test Name | Success Criteria | Methodology | Status | Responsible Engineer(s)
3.2.1.1 | Speed and Torque Requirement | Motor shall operate within speed range of 0RPM to 1800RPM and torque range of 0lb-ft to 0.729lb-ft. | Input motor with voltage and check if it achieves 0RPM and 0lb-ft . Repeat for 300RPM, 600RPM, 900RPM, 1200RPM, 1500RPM, 1800RPM. | Untested | Andrew, Ryan
3.2.1.2 | Frequency Requirement | System shall operate within frequency range of 10Hz to 60Hz. | Input system with frequency generator set to 5Hz and check if the motor runs smoothly. Repeat for 10Hz, 20Hz, 30Hz, 40Hz, 50Hz, 60Hz. | Untested | All
3.2.1.3 | Temperature Requirement | System shall operate within temperature range of 0˚C to 70˚C. | Place system in freezer set to 0˚C and check if the motor runs smoothly. Repeat with oven set to 70˚C. | Untested | All
3.2.3.2 | Input Voltage Level | System input voltage shall be 208VAC. | Measure with multimeter and check if the voltage is 208VAC. | Untested | Aidan
3.2.3.3 | Input Noise and Ripple | System shall not exceed ripple range of 0V to 0.165V. | Measure with multimeter and check if the voltage exceeds 0V to 0.165V. | Untested | Andrew
3.2.3.4 | External Commands | External commands shall be documented in appropriate ICD. | Show to teaching team and check with them for approval. | Untested | All
3.2.3.5 | Visual Output | Oscilloscope displays each of the three phases of the PWM sine wave. | Connect oscilloscope probes to the set output pins for the PWM signals, ensure that the signals' duty cycles span from 0-100% and are rougly separated by thirds. | Tested | Ryan
3.2.3.6 | Connectors | System shall use terminal blocks for power and signal connections. | Observe power and signal connections and check if they are are terminal blocks. | Untested | Mackenzie, Andrew, Aidan
3.2.3.7 | Overtemperature Shutdown | System shall automatically shut down if sensor exceeds temperature range of 0˚C to 70˚C. | Place sensor in freezer set to -1˚C and check if sensor is triggered. Repeat with oven set to 71˚C. | Untested | Mackenzie
3.2.3.8 | Built in Test | System shall generate and evaluate test signals to assess failure status. | Compare generated values with known values and check if the failure statuses match. Repeat for six additional sets of values. | Untested | All
3.2.3.9 | Optoelectronics Voltage Constraint | The optoelectronics subsystem shall convert the voltage it receives down to a voltage in the range of 15-20 V. | Test at full power where the opto receives ~60 V. Use a multimeter to measure voltage level on other side of opto barrier. | Tested | Mackenzie
3.2.3.10 | Digital to Power Continuity | The digital to power opto-isolators shall have a voltage of 0V across each component when connecting input to output. | Use a multimeter to ensure that the voltage across each digital isolator is zero. | Tested | Mackenzie
Paragraph # | Test Name | Success Criteria | Methodology | Status | Responsible Engineer(s)
3.2.3.11 | Power to Digital Continuity | The power to digital opto-isolators shall have a voltage of 0V across each component when connecting input to output | Use a multimeter to ensure that the voltage across each power isolator is zero. | Tested | Mackenzie
TBD | Inputs | The parameters are within the expected range. | Confirm that all electrical parameters (voltage, current, power) remain within safe and expected ranges under varying conditions. | Untested | All
TBD | Firmware Code Compiles | MPLab firmware successfully compiles without errors or warnings | Attempt to compile code in MPLab and examine output logs to check for errors or warnings | Tested | Ryan
TBD | Controller Performance | Motor spins according to user defined parameters. | Validate that the system operates efficiently and delivers accurate motor control across the expected range of operating conditions. | Untested | All
TBD | MCU Voltage Step Down | MCU converts the voltage it is given to 3.3V. | Measure the voltage of the signals being sent to the MCU and measure that the MCU converts it to 3.3V. | Untested | Mackenzie, Andrew
TBD | Rectifier Full System | System input voltage shall be rectified from 208VAC to 295VDC. | Measure with multimeter and check if the voltage after the rectifier is 295VDC. | Untested | Aidan
TBD | Rectifier Power Subsystem | System input voltage shall be rectified from 5VAC to 7.1 VDC. | Input 5VAC at differing angles of 120˚ on three waveform generators. Measure with multimeter and check if the voltage after the rectifier is 7.1 VDC. | Tested | Aidan
TBD | Isolated 15V Conversion | System shall convert 15VDC to isolated 15VDC. | Input 15VDC on a dc power supply. Measure with multimeter and check if the voltage after the converter is 15VDC. | Tested | Aidan
TBD | Isolated 5V Conversion | System shall convert 3.3VDC to isolated 5VDC. | Input 3.3VDC on a dc power supply. Measure with multimeter and check if the voltage after the converter is 5VDC. | Untested | Aidan
TBD | User Interface | User is able to change the speed of the rotating PWM values by turning the potentiometer. | Change potentiometer position to lowest, highest, and middle notch to observe that the target frequency of the system is close to 60, 10, and 35 respectively, and the rotating PWM values change pace accordingly | Tested | Ryan
TBD | Frequency Testing | Code properly changes the frequency of the PWM signals | Use oscilloscope or a timer to measure the PWM waves to ensure that the program's target frequency is similar to the actual frequency of the PWM signals. | Tested | Ryan
TBD | Debugger Connection | The Microcontroller shall be able to properly communicate with Pickit4 debugger | Connect the Pickit4 Debugger to microcontroller PCB using the 5 pin connector and ensure that MPLAB X IDE can recognize the device. | Untested | Andrew
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

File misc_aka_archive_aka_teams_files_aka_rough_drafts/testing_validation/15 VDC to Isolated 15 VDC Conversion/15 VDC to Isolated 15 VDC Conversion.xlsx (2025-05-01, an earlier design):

Vin (V) | Vin,pp (mV) | Vout (V) | Vout,pp (mV) | Screenshot | Iout (mA) | Vout (V)
9.1 | 200 | 15.1 | 400 |  | 12 | 14.959
15.1 | 500 | 15.0 | 400 |  | 25 | 14.951
20.9 | 500 | 14.9 | 400 |  | 50 | 14.937
27.0 | 500 | 15.3 | 500 |  | 75 | 14.924
33.040 | 578 | 14.887 | 264 |  | 100 | 14.912
35.804 | 503 | 14.887 | 264 |  | 125 | 14.898
 |  |  |  |  | 134 | 14.893

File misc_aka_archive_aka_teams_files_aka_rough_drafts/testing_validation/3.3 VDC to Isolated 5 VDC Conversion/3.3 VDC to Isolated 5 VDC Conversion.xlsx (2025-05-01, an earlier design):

Vin (V) | Vin,pp (mV) | Vout (V) | Vout,pp (mV) | Screenshot | Iout (mA) | Vout (V)
2.8 | 500 | 4.9 | 500 |  | 12 | 5.381
3.2 | 500 | 4.8 | 500 |  | 50 | 5.188
3.3 | 500 | 5.3 | 500 |  | 100 | 4.981
3.6 | 900 | 5.7 | 500 |  | 150 | 4.782
 |  |  |  |  | 200 | 4.581

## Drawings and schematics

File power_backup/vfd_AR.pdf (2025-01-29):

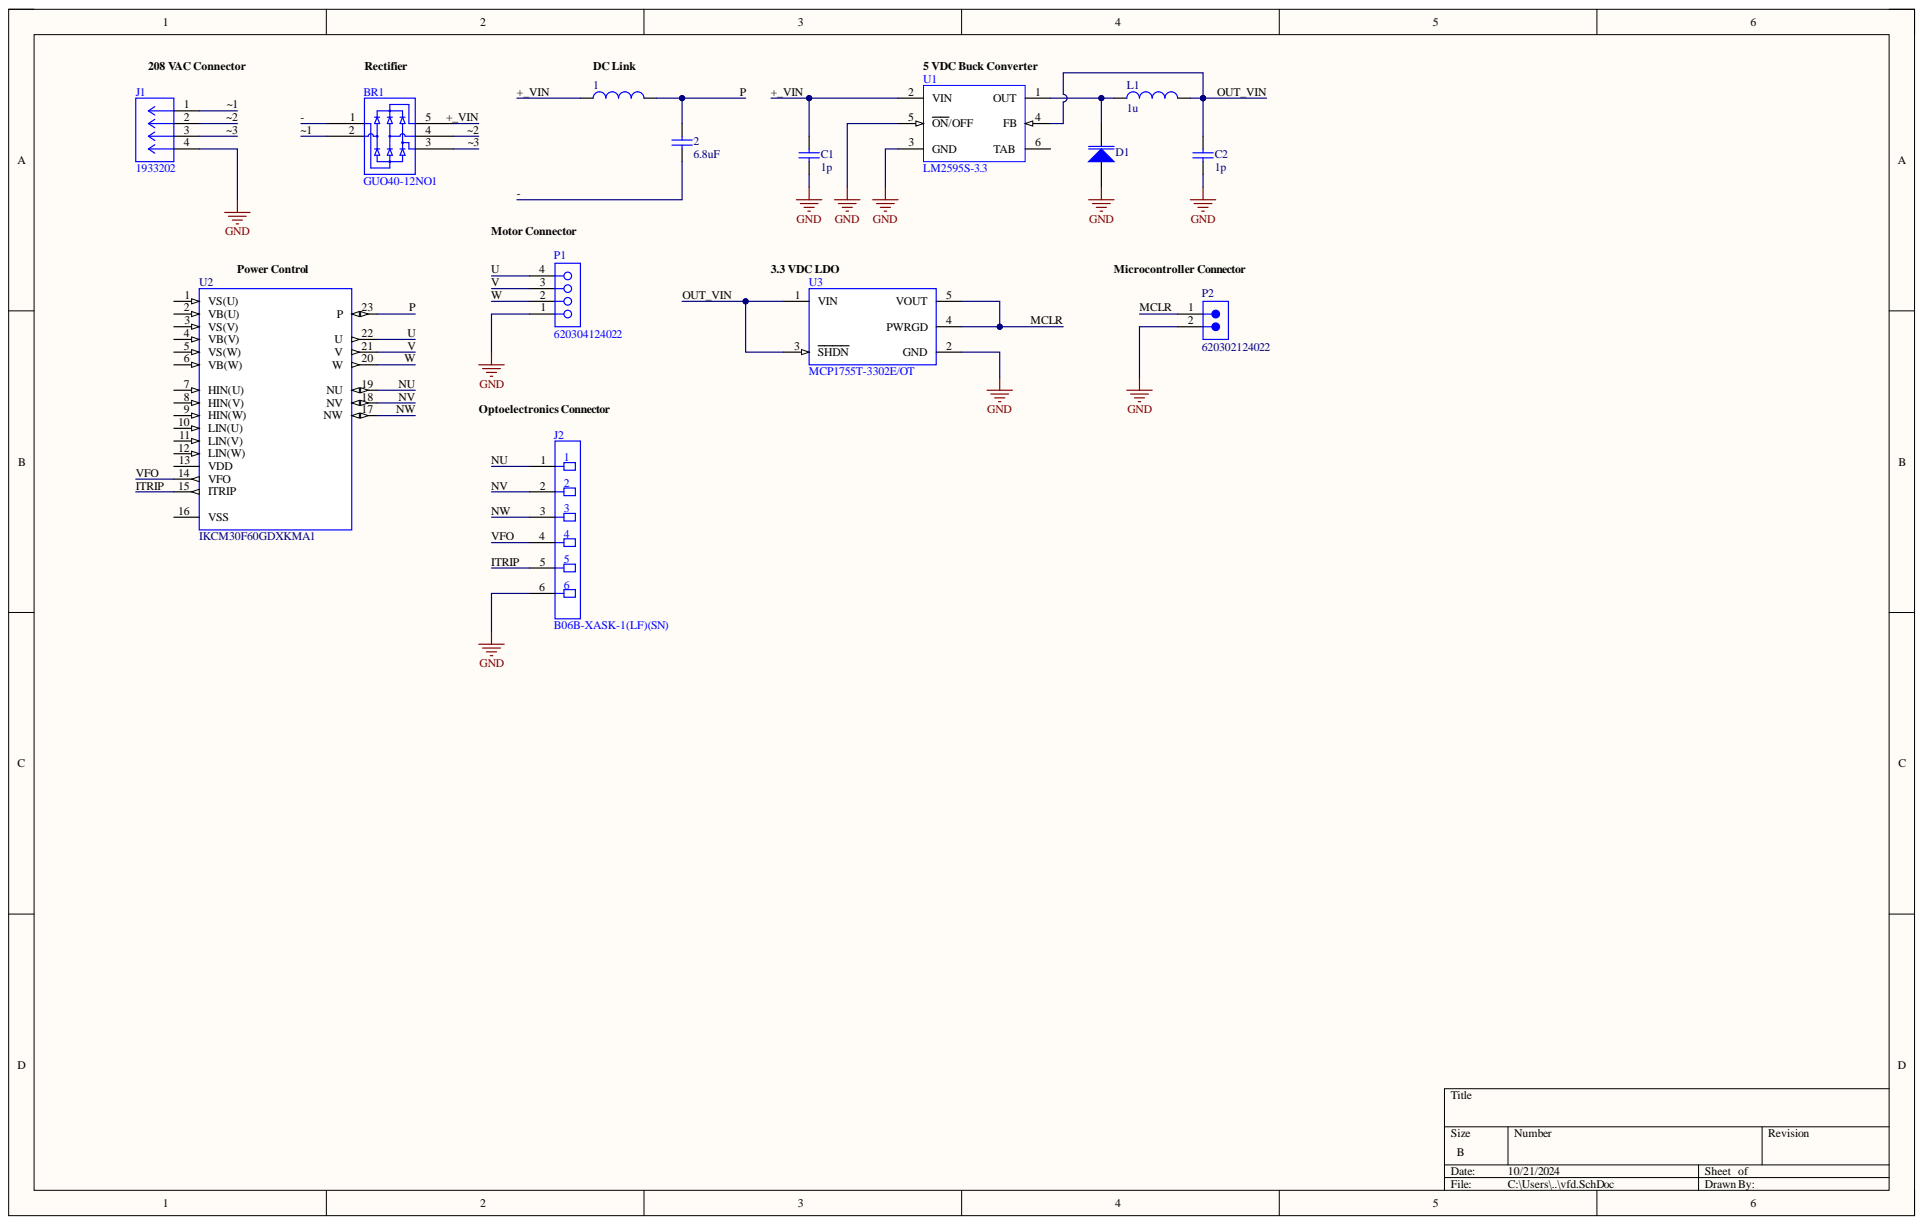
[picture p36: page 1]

Size B | Number | Revision

Date: 10/21/2024 | Sheet of
File: C:\Users\..\vfd.SchDoc | Drawn By:

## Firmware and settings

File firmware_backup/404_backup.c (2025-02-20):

#include "mcc_generated_files/system/system.h"
#include "mcc_generated_files/system/pins.h"
#include "mcc_generated_files/adc/adc1.h"
#include "mcc_generated_files/pwm/sccp1.h"
#include "mcc_generated_files/pwm/sccp3.h"
#include "mcc_generated_files/pwm/sccp2.h"
#include "mcc_generated_files/pwm/sccp4.h"
#include "mcc_generated_files/pwm/sccp5.h"
#include "mcc_generated_files/pwm/sccp6.h"

#define FCY 4000000UL  // Assuming Fosc = 8 MHz, FCY = Fosc / 2

#include <libpic30.h>
#include <stdbool.h>
#include <stdint.h>
#include <math.h>

#define TABLE_SIZE 512  // Define the number of points in the sine table
#define PWM_MAX 4095    // Max PWM value for 12-bit resolution
#define M_PI 3.14159265358979323846
#define PWM_FREQUENCY 1000  // Frequency that the PWM was set to (Hertz)

uint16_t potValue;
uint16_t dutyCycle;
bool system_running = false; // System starts in "stopped" mode

uint16_t sine_table[TABLE_SIZE];
uint16_t phase_offset_a_high = 0;
uint16_t phase_offset_b_high = TABLE_SIZE / 3;
uint16_t phase_offset_c_high = (2 * TABLE_SIZE) / 3;
uint16_t phase_offset_a_low;
uint16_t phase_offset_b_low;
uint16_t phase_offset_c_low;

uint16_t map(uint16_t x, uint16_t in_min, uint16_t in_max, uint16_t out_min, uint16_t out_max) {
    return (uint16_t)(((uint32_t)(x - in_min) * (out_max - out_min)) / (in_max - in_min) + out_min);
}

// Function to initialize the sine table
void initialize_sine_table() {
    for (int i = 0; i < TABLE_SIZE; i++) {
        float angle = (2 * M_PI * i) / TABLE_SIZE;
        sine_table[i] = (uint16_t)((sin(angle) * 0.5 + 0.5) * PWM_MAX);
    }
}

// Function to calculate step increment
uint16_t calculate_step_increment(uint16_t potValue) {
    uint16_t target_freq = map(potValue, 0, 4096, 10, 60);
    printf("Target Frequency: %u\n\r", target_freq);
    return (uint16_t)((TABLE_SIZE * target_freq) / PWM_FREQUENCY);
}

// Function to set three-phase PWM signals
void set_three_phase_pwm(uint16_t potValue) {
    uint16_t duty_a = sine_table[phase_offset_a_high % TABLE_SIZE];
    uint16_t duty_b = sine_table[phase_offset_b_high % TABLE_SIZE];
    uint16_t duty_c = sine_table[phase_offset_c_high % TABLE_SIZE];

    uint16_t duty_a_low = sine_table[phase_offset_a_low % TABLE_SIZE];
    uint16_t duty_b_low = sine_table[phase_offset_b_low % TABLE_SIZE];
    uint16_t duty_c_low = sine_table[phase_offset_c_low % TABLE_SIZE];

    duty_a = (uint16_t)(0.8 * duty_a + 0.1 * PWM_MAX);
    duty_b = (uint16_t)(0.8 * duty_b + 0.1 * PWM_MAX);
    duty_c = (uint16_t)(0.8 * duty_c + 0.1 * PWM_MAX);

    duty_a_low = (uint16_t)(0.8 * duty_a_low + 0.1 * PWM_MAX);
    duty_b_low = (uint16_t)(0.8 * duty_b_low + 0.1 * PWM_MAX);
    duty_c_low = (uint16_t)(0.8 * duty_c_low + 0.1 * PWM_MAX);

    PWM1_DutyCycleSet(system_running ? duty_a : 0);
    PWM2_DutyCycleSet(system_running ? duty_b : 0);
    PWM3_DutyCycleSet(system_running ? duty_c : 0);
    PWM4_DutyCycleSet(system_running ? duty_a_low : 0);
    PWM5_DutyCycleSet(system_running ? duty_b_low : 0);
    PWM6_DutyCycleSet(system_running ? duty_c_low : 0);

    uint16_t step_increment = calculate_step_increment(potValue);
    phase_offset_a_high = (phase_offset_a_high + step_increment) % TABLE_SIZE;
    phase_offset_b_high = (phase_offset_b_high + step_increment) % TABLE_SIZE;
    phase_offset_c_high = (phase_offset_c_high + step_increment) % TABLE_SIZE;
    phase_offset_a_low = (phase_offset_a_low + step_increment) % TABLE_SIZE;
    phase_offset_b_low = (phase_offset_b_low + step_increment) % TABLE_SIZE;
    phase_offset_c_low = (phase_offset_c_low + step_increment) % TABLE_SIZE;
}

// Function to check button press and toggle system state
void check_button_press() {
    static bool button_pressed = false;
    
    if (BUTTON1_GetValue() == 0) {  // Button pressed (active-low)
        __delay_ms(50);  // Debounce delay
        if (BUTTON1_GetValue() == 0 && !button_pressed) {
            system_running = !system_running;  // Toggle system state
            button_pressed = true;  // Prevent multiple toggles
            printf("System %s\n\r", system_running ? "Started" : "Stopped");
        }
    } else {
        button_pressed = false;  // Reset flag when button is released
    }
}

int main(void) {
    SYSTEM_Initialize();
    initialize_sine_table();

    phase_offset_a_low = phase_offset_a_high + (TABLE_SIZE / 2);
    phase_offset_b_low = phase_offset_b_high + (TABLE_SIZE / 2);
    phase_offset_c_low = phase_offset_c_high + (TABLE_SIZE / 2);

    __delay_ms(25);

    printf("Hello, World!\r\n");

    while (1) {
        check_button_press();  // Check if button is pressed to toggle system

        if (system_running) {
            if (ADC1_IsConversionComplete(POT_PIN)) {
                potValue = ADC1_ConversionResultGet(POT_PIN);
                printf("Pot: %d, ", potValue);
                set_three_phase_pwm(potValue);
            } else {
                printf("ADC conversion not complete.\r\n");
            }
        }
    }
}

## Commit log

2025-01-13 Create 403 Code
    Working development board code from first semester of capstone (403)
2025-01-30 mackenzie file backup
    [mackenziemillerschem1.SchDoc, mackenziepcbpcbrev2.PcbDoc]
2025-02-22 pcbv1 backup
    [vfd_power_v1.PcbDoc, vfd_power_v1.PrjPcb, vfd_power_v1.SchDoc]
2025-02-22 power backup
    [vfd_power_v1.GBL, vfd_power_v1.GBO, vfd_power_v1.GBP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]
2025-04-30 teams files upload
    [404_Decision_Matrix.xlsx]
